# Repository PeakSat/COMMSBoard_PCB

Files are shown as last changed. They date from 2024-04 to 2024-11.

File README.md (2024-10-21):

# SatNOGS COMMS hardware

A CubeSat format ([LibreCube Board](https://wiki.librecube.org/index.php?title=LibreCube_Board_Specification)) COMMS board.
It supports UHF and S-Band concurrent half duplex (in each band) communication.
More details could be found [here](https://gitlab.com/librespacefoundation/satnogs-comms/satnogs-comms-design-doc).

Stable versions are tagging with TBD.

## Contribute
This is a KiCAD project thus merging can be tricky.
Coordinate with project engineers before starting any changes and take look at issues.

## EDA
KiCAD 6

Requires [lsf-kicad-lib](https://gitlab.com/librespacefoundation/lsf-kicad-lib) to be installed.
Set path LSF_KICAD_LIB to point to lsf-kicad-lib folder for 3D models to appear correctly

#### Schematic
Changes in manufacturer part numbers field, footprints and designators can be merged most of the times.
Any part change, change in placement, wire placement etc cannot be merged at this point.

One exception is Hierarchical sheets provided that:

* A single person is working on a Hierarchical sheet
* Annotation is using sheet number
* Global nets are respected
* Changes in Hierarchical labels are coordinated

#### PCB
At this point any merging on PCB files must be avoided.
Also for the PCB (*.kicad_pcb) is used [LFS](https://docs.gitlab.com/ee/topics/git/lfs/) to prevent
a large size repository and to use the feature of LFS lock. The LFS lock protects the developers
to have conflicts in PCB that aren't merged. For that reason use:

```
git lfs clone
```

to clone the repository.

## Simulation
[Qucs 0.0.20](https://github.com/Qucs/qucs).

## License
Licensed under the [CERN OHLv1.2](LICENSE)


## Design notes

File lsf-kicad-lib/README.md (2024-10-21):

## Libre Space Foundation KiCad Library

This repository contains the schematic, footprint and 3D libraries maintained by the LSF KiCad library team.

Most designed from scratch. Some 3D models are Hirose downloads, and [Smisioto's](http://smisioto.no-ip.org/elettronica/kicad/kicad-en.htm) released under CC-BY-SA v3

## Usage
Clone lsf-kicad-lib and import symbol and footprint libraries to your KiCad installation  
Under `Preferences -> Configure Path` set a new environment variable named `LSF_KICAD_LIB` and set the path to the location where lsf-kicad-lib is cloned  

## Contributing
Unless you are contributing to an LSF hardware project, please consider contributing directly to [KiCad libraries](https://gitlab.com/kicad)  
Please adhere to [KLC](https://klc.kicad.org/) when creating components  
Footprint 3D models should have a path prefix of `${LSF_KICAD_LIB}/lsf-kicad-lib.3dshapes/` so a complete path would look like `${LSF_KICAD_LIB}/lsf-kicad-lib.3dshapes/One_Small_Step_For_Man-size_9.5in.wrl`

lsf-kicad-lib uses CI to test against [KLC](https://klc.kicad.org/), if CI fails but component is correct please justify the reason in your merge request

## License

Licensed under the [Creative Commons CC-BY-SA 4.0 License](LICENSE) or as referenced.

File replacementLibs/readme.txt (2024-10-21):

Miniciruits BPJC-252R+ bandpass filter footprint to be added upon creation
Add x2 new mosfet to the one channel one as well
RPL x2

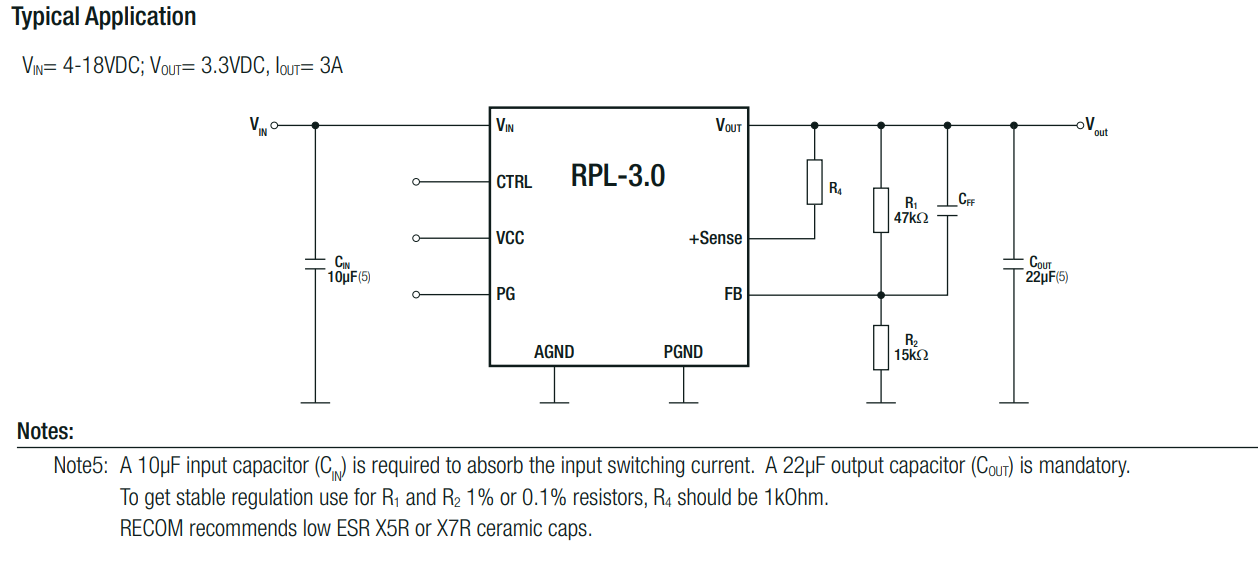
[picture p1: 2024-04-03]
3d_sources/RTL.PNG

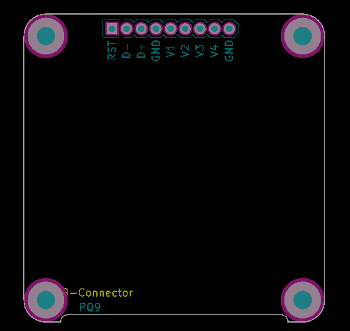
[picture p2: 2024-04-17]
lsf-kicad-lib/templates/PQ9/meta/board.png

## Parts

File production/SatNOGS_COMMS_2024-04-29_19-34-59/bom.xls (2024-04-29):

Designator,Footprint,Quantity,Value,LCSC Part #
ANT-S901,MMCX_Molex_73415-0961_Horizontal_1.6mm-PCB,1,RF 24,
ANT-U1001,MMCX_Molex_73415-0961_Horizontal_1.6mm-PCB,1,RF 09,
C1,0402,1,470n,
C1001, C1002, C1004, C1006, C1011, C1013, C1018, C1020, C1021, C1022, C1024, C1025, C1026, C1028, C1032, C1038, C1039, C1042, C1047, C1049, C1052, C1055, C612, C613, C616, C619,0402,26,100p,
C1003, C1005, C1010, C1012, C1017, C1019, C1023, C1030, C1048, C1053, C1054, C2, C31, C402, C403, C406, C408, C409, C410, C411, C412, C413, C415, C418, C501, C502, C603, C604, C605, C607, C608, C609, C701, C702, C703,0402,35,100n,
C1007, C1008, C1009, C1014, C1016, C1037, C601,0402,7,1n,
C1015,0603,1,220pF,
C1027,0402,1,2p,
C1029, C1034, C1035,0402,3,10n,
C1031,0402,1,62p,
C1036,T495C,1,10u,
C1040,0402,1,24p,
C1043,0402,1,3.3p,
C1046, C606, C610, C611,0402,4,1u,
C1050, C1051, C504,0805,3,10u,
C17, C18, C19, C20, C21, C6,0603,6,1n,
C201, C202, C531, C9,0603,4,100n,
C23, C24, C25, C27, C28, C3,0805,6,22uF,
C29, C7,0805,2,6.8u,
C404, C405, C407,1206,3,4.7u,
C419, C420,1206,2,2.2u,
C421, C422,0402,2,12p,
C5,0603,1,10u,
C506, C512,0805,2,100n,
C510,0402,1,2.2n,
C513, C516,0805,2,22u,
C529, C533,0603,2,1u,
C602,0402,1,10p,
D401,0402,1,PE14,
D402,0402,1,PE15,
D501,0805,1,3.6V,
D502,0402,1,3V3,
FB1001, FB401,0603,2,Ferrite_Bead,
FID1, FID2, FID3, FID4, FID5, FID6,Fiducial_1mm_Mask2mm,6,Fiducial,
FL2,SF2446E,1,SF2446E,
IC1,B1601,1,B1601,
J1, J2,Molex_Pico-Lock_504050-0491_1x04-1MP_P1.50mm_Horizontal,2,Conn_01x04,
J102,ESQ-126-39-x-D,1,Η1,
J103,ESQ-126-39-x-D,1,Η2,
L1001, L1002,0402,2,120n,
L1003, L1005, L1009,0402,3,68n,
L1004,0402,1,3.2n,
L1006,0402,1,18n,
L1007,0402,1,8.2n,
L1008,0402,1,47n,
L2,L_Abracon_ASPI-0530HI,1,2.2u,
L3,0805,1,0u,
L501,L_Bourns_SRN6045TA,1,4.7u,
Q1, Q2,SQJ910AEPT1_GE3,2,SQJB90EP-T1_GE3,
Q3,SOT95P230X110-3N,1,PMV28XPEAR,
Q401,SOT-23,1,FDN308P,
R1, R1030, R1031, R402, R605,0402,5,100k,
R10, R1004, R1005, R1006, R1007, R1008, R1009, R1012, R1014, R1020, R1021, R1022, R1024, R405, R606,0402,15,0,
R1001, R1002,0402,2,82,
R1003,0402,1,52.3,
R1010, R1011, R1029, R11, R3, R4, R406, R509, R533, R534, R6, R603, R8, R9,0402,14,10k,
R1013, R1015, R1023, R401,0402,4,1k,
R1016,0402,1,412,
R1017,0402,1,240,
R1019,0402,1,280,
R1025,0402,1,2.2k,
R1028,0402,1,33k,
R1032,0402,1,374k,
R1033,0402,1,110k,
R12, R407,0402,2,DNP,
R13, R14, R17, R18,0402,4,5k,
R15, R16, R502, R504, R507,0603,5,100k,
R2,0402,1,18.2k,
R201, R202, R522,0603,3,10k,
R203, R204,0603,2,120,
R403,0402,1,4.7k,
R5,0402,1,25.5k,
R501,0603,1,200k,
R503,0603,1,345k,
R508,0603,1,620k,
R510,0603,1,73.2k,
R513,0603,1,706k,
R515, R516,0603,2,2.2k,
R520,0603,1,30,
R521,0603,1,30.9k,
R529, R530, R531, R532,0805,4,0.02,
R537,0402,1,330,
R604,0402,1,470,
R7,0402,1,4.87k,
R701, R702, R703,0402,3,500,
RN401,R_Array_Convex_2x0402,1,330,
RN601,R_Array_Convex_4x0402,1,470,
RN603,R_Array_Convex_2x0402,1,R_Pack02,
T1001, T1002,ATB2012,2,Transformer_1P_1S,
U1,LQFP-100_14x14mm_P0.5mm,1,STM32H743VITx,
U1001,QFN-16-1EP_4x4mm_P0.65mm_EP2.1x2.1mm_ThermalVias,1,AD8318,
U1002,LFCSP-24-1EP_4x4mm_P0.5mm_EP2.3x2.3mm_ThermalVias,1,ADL5330,
U1003, U1004,Fairchild_MicroPak-6_1.0x1.45mm_P0.5mm,2,NC7SB3157L6X,
U1006,QFN-24-1EP_4x4mm_P0.5mm_EP2.7x2.7mm_ThermalVias,1,TQP7M9106,
U1009,DFN-8-1EP_2x2mm_P0.5mm_EP1.05x1.75mm,1,TSV912IQ2T,
U1012,GE0805C-2,1,LFCG-490+,
U1013,DFN-8-1EP_2x2mm_P0.5mm_EP0.7x1.6mm,1,TQP3M9036,
U1014, U603,SOT-553,2,NL17SV04XV5T2G,
U1015,GE0805C-2,1,LFCG-1400+,
U1016, U1017,MLP-8,2,FPF2701,
U1018,IDT_NEG-12-1EP_2x2mm_P0.5mm_EP1.1x1.1mm_ThermalVias,1,F2972,
U3,Texas_VQFN-10-HR_2x2_Pitch0.5mm,1,TPS62913,
U4, U5,SOT-23-8,2,TCAN337G,
U401,BGA-153_13.0mmx11.5mm_P0.5mm,1,SDINBDG4-8G,
U404,OSC_ECS-TXO-2520-33-120-AN-TR,1,ECS-TXO-2520-33-120-AN-TR,
U501, U502,Maxim_T833-2_TDFN-8-1EP_3x3mm_P0.65mm_EP1.5x2.3mm,2,MAX6497,
U504,SOT-23-6,1,TPS56339,
U508,WSON-6-1EP_2x2mm_P0.65mm_EP1x1.6mm_ThermalVias,1,LP5912-3.3DRV,
U509,Texas_RGV_S-PVQFN-N16_EP2.1x2.1mm,1,INA3221,
U6,QFN-14-1EP_1.60x1.60mm_P0.40mm_EP0.74x0.74mm,1,SKY13421-486LF,
U601,KT1612,1,KT1612A,
U602,QFN-48-1EP_7x7mm_P0.5mm_EP5.6x5.6mm,1,AT86RF215,
U701, U702, U703,WSON-6-1EP_2x2mm_P0.65mm_EP1x1.6mm,3,TMP117,
Y401,Crystal_SMD_3215-2Pin_3.2x1.5mm,1,32768Hz,

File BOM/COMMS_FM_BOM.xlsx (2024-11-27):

Designator | Footprint | Quantity | Value
ANT-S901 | MMCX_Molex_73415-0961_Horizontal_1.6mm-PCB | 1 | RF 24 | 73415-0961 (https://gr.mouser.com/ProductDetail/Molex/73415-0961?qs=LDM2r2BBpnbP9ohwHUReTQ%3D%3D)
ANT-U1001 | MMCX_Molex_73415-0961_Horizontal_1.6mm-PCB | 1 | RF 09 | 73415-0961 (https://gr.mouser.com/ProductDetail/Molex/73415-0961?qs=LDM2r2BBpnbP9ohwHUReTQ%3D%3D)
C1 | 402 | 1 | 2.2u | MSAST105CB5225KFNA01 (https://eu.mouser.com/ProductDetail/TAIYO-YUDEN/MSAST105CB5225KFNA01?qs=tlsG%2FOw5FFgp%2Fj%252BcBdp0SQ%3D%3D)
C1001, C1002, C1004, C1006, C1011, C1013, C1018, C1020, C1021, C1022, C1024, C1025, C1026, C1028, C1032, C1038, C1039, C1042, C1047, C1049, C1052, C1055, C612, C613, C616, C619 | 0402 | 26 | 100p | CBR04C101J3GAC (https://gr.mouser.com/ProductDetail/KEMET/CBR04C101J3GAC?qs=kpVq%2FgIAs50lnV8B4851AQ%3D%3D)
C1003, C1005, C1010, C1012, C1017, C1019, C1023, C1030, C1048, C1053, C1054, C2, C31, C402, C403, C406, C408, C409, C410, C411, C412, C413, C415, C418, C501, C502, C603, C604, C605, C607, C608, C609, C701, C702, C703 | 0402 | 35 | 100n | C0402C104K4RACTU (https://gr.mouser.com/ProductDetail/KEMET/C0402C104K4RACTU?qs=DBJr%252BvBUjU54jK7d4uAeew%3D%3D)
C1007, C1008, C1009, C1014, C1016, C1037, C601 | 0402 | 7 | 1n | C0402C102K8RACAUTO (https://gr.mouser.com/ProductDetail/KEMET/C0402C102K8RACAUTO?qs=PqoDHHvF64%252Bcvfiy0YO9RQ%3D%3D)
C1015 | 0603 | 1 | 220pF | CL10C221JB8NNNC (https://gr.mouser.com/ProductDetail/Samsung-Electro-Mechanics/CL10C221JB8NNNC?qs=349EhDEZ59pzGXg3weaqwg%3D%3D)
C1027 | 0402 | 1 | 2p | GJM1555C1H2R0WB01D (https://gr.mouser.com/ProductDetail/Murata-Electronics/GJM1555C1H2R0WB01D?qs=YLLXL5qGyDstO156VbiHGA%3D%3D)
C1029, C1034, C1035 | 0402 | 3 | 10n | C0402C103K9RACTU (https://gr.mouser.com/ProductDetail/KEMET/C0402C103K9RACTU?qs=DBJr%252BvBUjU6xorlRi5IJdg%3D%3D)
C1031 | 0402 | 1 | 62p | 04025A620FAT2A (https://gr.mouser.com/ProductDetail/KYOCERA-AVX/04025A620FAT2A?qs=Wf75Zj%252Bm1TOgugGJIn7eTg%3D%3D)
C1036 | T495C | 1 | 10u | T495C106K035ATE400 (https://gr.mouser.com/ProductDetail/KEMET/T495C106K035ATE400?qs=MYVaeE1wThLltmp5qaw8IA%3D%3D)
C1040 | 0402 | 1 | 24p | 04025U240FAT2A (https://gr.mouser.com/ProductDetail/KYOCERA-AVX/04025U240FAT2A?qs=ZwvTZoB9SO%2FwGwGLwPpjgw%3D%3D)
C1043 | 0402 | 1 | 3.3p | GJM1555C1H3R3WB01D (https://gr.mouser.com/ProductDetail/Murata-Electronics/GJM1555C1H3R3WB01D?qs=YLLXL5qGyDt2ejtN1v%252B1AA%3D%3D)
C1046, C606, C610, C611 | 0402 | 4 | 1u | C0402C105K8PAC7411 (https://gr.mouser.com/ProductDetail/KEMET/C0402C105K8PAC7411?qs=2FIyTMJ0hNmV%2F7SAMXtJQQ%3D%3D)
C1050, C1051, C504 | 0805 | 3 | 10u | EMK212BB7106KG-T (https://gr.mouser.com/ProductDetail/TAIYO-YUDEN/EMK212BB7106KG-T?qs=vF%252B8ahGVilemLVRka0hELA%3D%3D)
C17, C18, C19, C20, C21, C6 | 0603 | 6 | 1n | C0603X102K5GACAUTO (https://gr.mouser.com/ProductDetail/KEMET/C0603X102K5GACAUTO?qs=Rp5uXu7WBW%2FQ943CZtK%2F6w%3D%3D)
C201, C202, C531, C9 | 0603 | 4 | 100n | C0603C104K9RACTU (https://gr.mouser.com/ProductDetail/KEMET/C0603C104K9RACTU?qs=7q2aiX3GdliuPZzPpldOsA%3D%3D)
C23, C24, C25, C27, C28, C3 | 0805 | 6 | 22uF | GRM21BR61A226ME44L (https://gr.mouser.com/ProductDetail/Murata-Electronics/GRM21BR61A226ME44L?qs=eeBpzGFlv%252B8tSfxib2AMhw%3D%3D)
C29, C7 | 0805 | 2 | 6.8u | C2012X5R1E685K125AC (https://gr.mouser.com/ProductDetail/TDK/C2012X5R1E685K125AC?qs=LcTL%2F5vFEzGU8HZPTu5zsg%3D%3D)
C404, C405, C407 | 1206 | 3 | 4.7u | TAJA475K016R (https://gr.mouser.com/ProductDetail/KYOCERA-AVX/TAJA475K016RNJ?qs=QtLZGLLAmDYIMcNbe5r3xw%3D%3D)
C419, C420 | 1206 | 2 | 2.2u | AC1206KKX7R7BB225 (https://gr.mouser.com/ProductDetail/YAGEO/AC1206KKX7R7BB225?qs=eP2BKZSCXI6d%2Fne9Jk0GEA%3D%3D)
C421, C422 | 0402 | 2 | 12p | CBR04C120F3GAC (https://gr.mouser.com/ProductDetail/KEMET/CBR04C120F3GAC?qs=kpVq%2FgIAs52ttHbXJFjLsg%3D%3D)
C5 | 0603 | 1 | 10u | EMK107BC6106MA-T (https://gr.mouser.com/ProductDetail/TAIYO-YUDEN/EMK107BC6106MA-T?qs=VWNNG7jHlrLjpV1w%2FJc9eQ%3D%3D)
C506, C512 | 0805 | 2 | 100n | C0805C104M5RACTU (https://gr.mouser.com/ProductDetail/KEMET/C0805C104M5RACTU?qs=VOOUd%252Bza08qHu13WgNByHQ%3D%3D)
C510 | 0402 | 1 | 2.2n | CGA2B2X7R1H222K050BA (https://gr.mouser.com/ProductDetail/TDK/CGA2B2X7R1H222K050BA?qs=NRhsANhppD%2Fb%2FoKooR%252BeFw%3D%3D)
C513, C516 | 0805 | 2 | 22u | GRM21BR61A226ME44L (https://gr.mouser.com/ProductDetail/Murata-Electronics/GRM21BR61A226ME44L?qs=eeBpzGFlv%252B8tSfxib2AMhw%3D%3D)
C529, C533 | 0603 | 2 | 1u | EMK107B7105KA-T (https://gr.mouser.com/ProductDetail/TAIYO-YUDEN/EMK107B7105KA-T?qs=I6KAKw0tg2zS1zj87Lm%2FxQ%3D%3D)
C602 | 0402 | 1 | 10p | C0402C100C8GACTU (https://gr.mouser.com/ProductDetail/KEMET/C0402C100C8GACTU?qs=v7s4VpRpa0t2l6BHkID7%2Fw%3D%3D)
D401 | 0402 | 1 | PE14 | FHA1105P-TR (https://gr.mouser.com/ProductDetail/Stanley-Electric/FHA1105P-TR?qs=byeeYqUIh0MAYVMdncV%252BvA%3D%3D)
D402 | 0402 | 1 | PE15 | FHA1105P-TR (https://gr.mouser.com/ProductDetail/Stanley-Electric/FHA1105P-TR?qs=byeeYqUIh0MAYVMdncV%252BvA%3D%3D)
D501 | 0805 | 1 | 3.6V | BZY55B3V6 RBG (https://gr.mouser.com/ProductDetail/Taiwan-Semiconductor/BZY55B3V6-RBG?qs=mAH9sUMRCtv1hjtg7HbTxw%3D%3D)
D502 | 0402 | 1 | 3V3 | APHHS1005LQBC/D-V (https://gr.mouser.com/ProductDetail/Kingbright/APHHS1005LQBC-D-V?qs=WbpYJYa8y32aFVn6IIj1Dg%3D%3D)
FB1001, FB401 | 0603 | 2 | Ferrite_Bead | BLM18KG331SN1D (https://gr.mouser.com/ProductDetail/Murata-Electronics/BLM18KG331SN1D?qs=rvfpa0%252BU10NzC2vi4JWfgQ%3D%3D)
FL2 | RF1419D | 1 | RF1419D | RF1419D (https://gr.mouser.com/ProductDetail/RFMi/RF1419D?qs=zW32dvEIR3tUQ4hxASYaKw%3D%3D)
IC1 | B1601 | 1 | Orion B16 | GNSS module | Comment: To be placed only on the FM
J1, J2 | Molex_Pico-Lock_504050-0491_1x04-1MP_P1.50mm_Horizontal | 2 | Conn_01x04 | 504050-0491 (https://gr.mouser.com/ProductDetail/Molex/504050-0491?qs=yXHQdf%252Bjwlut3yyE1%252ByhMA%3D%3D)
J102 | ESQ-126-39-x-D | 1 | Η1 | ESQ-126-48-G-D-LL (https://www.digikey.lu/en/products/detail/samtec-inc/ESQ-126-48-G-D-LL/7094695)
J103 | ESQ-126-39-x-D | 1 | Η2 | ESQ-126-48-G-D-LL (https://www.digikey.lu/en/products/detail/samtec-inc/ESQ-126-48-G-D-LL/7094695)
L1001, L1002 | 0402 | 2 | 120n | LQG15WHR12G02D (https://gr.mouser.com/ProductDetail/Murata-Electronics/LQG15WHR12G02D?qs=rkhjVJ6%2F3EIx7JCOrOt0jQ%3D%3D)
L1003, L1005, L1009 | 0402 | 3 | 68n | MHQ1005P68NGTD25 (https://gr.mouser.com/ProductDetail/TDK/MHQ1005P68NGTD25?qs=J8wJ95O2yNKke5XTsKZiRQ%3D%3D)
L1004 | 0402 | 1 | 3.2n | LQG15WZ3N2B02D (https://gr.mouser.com/ProductDetail/Murata-Electronics/LQG15WZ3N2B02D?qs=rkhjVJ6%2F3EIZ%252BUOS4bnJ5g%3D%3D)
L1006 | 0402 | 1 | 18n | LQW15AN18NJ80D (https://gr.mouser.com/ProductDetail/Murata-Electronics/LQW15AN18NJ80D?qs=hNud%2FORuBR3MthCsSHMoHQ%3D%3D)
L1007 | 0402 | 1 | 8.2n | MHQ1005P8N2GT000 (https://gr.mouser.com/ProductDetail/TDK/MHQ1005P8N2GT000?qs=u4%252BEJ9urDAQClJN4T%2Ff%252BGw%3D%3D)
L1008 | 0402 | 1 | 47n | AISC-0402-47NG-T (https://gr.mouser.com/ProductDetail/ABRACON/AISC-0402-47NG-T?qs=dtFCtVqVXWePKsh6WPotjA%3D%3D)
L2 | L_Abracon_ASPI-0530HI | 1 | 2.2u | ASPI-0520LR-2R2M-T2 (https://gr.mouser.com/ProductDetail/ABRACON/ASPI-0520LR-2R2M-T2?qs=bWAYEm3xoCbh1TG6qbeZrA%3D%3D)
L3 | 0805 | 1 | 0u | 782853200 (https://gr.mouser.com/ProductDetail/Wurth-Elektronik/782853200?qs=sBf%2Fb4nBSle7OloWbfgdIw%3D%3D)
L501 | L_Bourns_SRN6045TA | 1 | 4.7u | SRN6045-4R7Y (https://gr.mouser.com/ProductDetail/Bourns/SRN6045-4R7Y?qs=opBjA1TV902tB4tumIiZhg%3D%3D)
Q1, Q2 | SQJ910AEPT1_GE3 | 2 | SQJB90EP-T1_GE3 | SQJB90EP-T1_GE3 (https://gr.mouser.com/ProductDetail/Vishay-Semiconductors/SQJB90EP-T1_GE3?qs=EBLjwc9jJJtSPXvpvmcSow%3D%3D)
Q3 | SOT95P230X110-3N | 1 | PMV28XPEAR | PMV28XPEAR (https://gr.mouser.com/ProductDetail/Nexperia/PMV28XPEAR?qs=W%2FMpXkg%252BdQ6VcRCVGMTksA%3D%3D)
Q401 | SOT-23 | 1 | FDN308P | FDN308P (https://gr.mouser.com/ProductDetail/onsemi-Fairchild/FDN308P?qs=GeD7q9OHBPyTnI9LJIlNJQ%3D%3D)
R1, R1030, R1031, R402, R605 | 0402 | 5 | 100k | CR0402-FX-1003GLF (https://gr.mouser.com/ProductDetail/Bourns/CR0402-FX-1003GLF?qs=URDPQ%2Fj0cz1ZruPSJQ7fsA%3D%3D)
R10, R1004, R1005, R1006, R1007, R1008, R1009, R1012, R1014, R1020, R1021, R1022, R1024, R405, R606 | 0402 | 15 | 0 | RC0402JR-070R (https://gr.mouser.com/ProductDetail/YAGEO/RC0402JR-070RP?qs=oypCK0zG324njv6h4dM%2FBg%3D%3D)
R1001, R1002 | 0402 | 2 | 82 | ERA-2AEB820X (https://gr.mouser.com/ProductDetail/Panasonic/ERA-2AEB820X?qs=YFwoyZoVY0jWB%2FWuuQzFhw%3D%3D)
R1003 | 0402 | 1 | 52.3 | RG1005P-52R3-B-T5 (https://gr.mouser.com/ProductDetail/Susumu/RG1005P-52R3-B-T5?qs=v5GkGT6DDHiy8ArKIHE1bw%3D%3D)
R1010, R1011, R1029, R11, R3, R4, R406, R509, R533, R534, R6, R603, R8, R9 | 0402 | 14 | 10k | CRCW040210K0FKEDC (https://gr.mouser.com/ProductDetail/Vishay-Dale/CRCW040210K0FKEDC?qs=E3Y5ESvWgWPiNLcGzwCGPg%3D%3D)
R1013, R1015, R1023, R401 | 0402 | 4 | 1k | CRCW04021K00FKEDC (https://gr.mouser.com/ProductDetail/Vishay-Dale/CRCW04021K00FKEDC?qs=E3Y5ESvWgWMj5mY%252BhDIyqg%3D%3D)
R1016 | 0402 | 1 | 412 | CRCW0402412RFKED (https://gr.mouser.com/ProductDetail/Vishay-Dale/CRCW0402412RFKED?qs=FaFwO5VmXOIp6VCgzV9Dxg%3D%3D)
R1017 | 0402 | 1 | 240 | CRCW0402240RFKEDC (https://gr.mouser.com/ProductDetail/Vishay-Dale/CRCW0402240RFKEDC?qs=E3Y5ESvWgWOlhgV8l94Qkw%3D%3D)
R1019 | 0402 | 1 | 280 | RC0402FR-07280RL (https://gr.mouser.com/ProductDetail/YAGEO/RC0402FR-07280RL?qs=f9DM49H8yrNOsmUU2z7A4A%3D%3D)
R1025 | 0402 | 1 | 2.2k | CRCW04022K20JNEDC (https://gr.mouser.com/ProductDetail/Vishay-Dale/CRCW04022K20JNEDC?qs=E3Y5ESvWgWOj5R%252BsplsFLw%3D%3D)
R1028 | 0402 | 1 | 33k | CR0402-FX-3302GLF (https://gr.mouser.com/ProductDetail/Bourns/CR0402-FX-3302GLF?qs=SFHnMgm9Isze0zS5GpsQzw%3D%3D)
R1032 | 0402 | 1 | 374k | CRCW0402374KFKED (https://gr.mouser.com/ProductDetail/Vishay-Dale/CRCW0402374KFKED?qs=1XGAtBqYNz57mwAP8KKAqw%3D%3D)
R1033 | 0402 | 1 | 110k | CRCW0402110KFKED (https://gr.mouser.com/ProductDetail/Vishay-Dale/CRCW0402110KFKED?qs=rlE3Te1NifyoK3%2FXIabNHA%3D%3D)
R12, R407 | 0402 | 2 | DNP
R13, R14, R17, R18 | 0402 | 4 | 5k | RC0402FR-075KL (https://gr.mouser.com/ProductDetail/YAGEO/RC0402FR-075KL?qs=9h0bZHM%2F3zL5adZvfm%252BR4Q%3D%3D)
R504 | 0603 | 1 | 100k | RN73H1JTTD1003F50 (https://eu.mouser.com/ProductDetail/KOA-Speer/RN73H1JTTD1003F50?qs=0hon8nwgHra%252Ba4k3Zp48xw%3D%3D)
R15, R16, R502, R504, R507 | 0603 | 5 | 100k | ERJ-3EKF1003V (https://gr.mouser.com/ProductDetail/Panasonic/ERJ-3EKF1003V?qs=H7k1u0Mp9JSqh2R2gj46DA%3D%3D)
R2 | 0402 | 1 | 18.2k | CRCW040218K2FKED (https://gr.mouser.com/ProductDetail/Vishay-Dale/CRCW040218K2FKED?qs=QPqDnsKvzKctMPTti4xZ7g%3D%3D)
R201, R202, R522 | 0603 | 3 | 10k | CRCW060310K0FKECC (https://gr.mouser.com/ProductDetail/Vishay-Dale/CRCW060310K0FKECC?qs=wd5RIQLrsJjYJGKL%252BLOtbQ%3D%3D)
R203, R204 | 0603 | 2 | 120 | ERJ-3EKF1200V (https://gr.mouser.com/ProductDetail/Panasonic/ERJ-3EKF1200V?qs=iBwFsHVUAOfkZ4Bj0qjBGg%3D%3D)
R403 | 0402 | 1 | 4.7k | CRCW04024K70FKEDC (https://gr.mouser.com/ProductDetail/Vishay-Dale/CRCW04024K70FKEDC?qs=E3Y5ESvWgWMhkkkEGGyyBQ%3D%3D)
R5 | 0402 | 1 | 25.5k | CRCW040225K5FKED (https://gr.mouser.com/ProductDetail/Vishay-Dale/CRCW040225K5FKED?qs=hD42E%2F8yzjq2MGDaErf%252BPQ%3D%3D)
R501 | 0603 | 1 | 200k | ERJ-H3ED2003V (https://gr.mouser.com/ProductDetail/Panasonic/ERJ-H3ED2003V?qs=eP2BKZSCXI7daGmcQhIBgg%3D%3D)
R503 | 0603 | 1 | 345k | RN731JTTD3443F100 (https://gr.mouser.com/ProductDetail/KOA-Speer/RN731JTTD3443F100?qs=F5djdNSOT4bwjyqVk7yJug%3D%3D)
R508 | 0603 | 1 | 620k | CPF0603B620KE (https://gr.mouser.com/ProductDetail/TE-Connectivity-Holsworthy/CPF0603B620KE?qs=gt1LBUVyoHkO9kiWGgxegA%3D%3D)
R510 | 0603 | 1 | 73.2k | RT0603FRE0773K2L (https://gr.mouser.com/ProductDetail/YAGEO/RT0603FRE0773K2L?qs=4Yf0coX8WGHmhZiQKKa7fg%3D%3D)
R513 | 0603 | 1 | 706k | RN73H1JTTD7063D100 (https://gr.mouser.com/ProductDetail/KOA-Speer/RN73H1JTTD7063D100?qs=VuQ0gRj%2FiB4rvIsmRvyBAA%3D%3D)
R515, R516 | 0603 | 2 | 2.2k | CR0603-JW-222ELF (https://gr.mouser.com/ProductDetail/Bourns/CR0603-JW-222ELF?qs=1ekQ6LclRXWKYqsntfXI1g%3D%3D)
R520 | 0603 | 1 | 30 | RC0603FR-0730RL (https://gr.mouser.com/ProductDetail/YAGEO/RC0603FR-0730RL?qs=0yPvnVz5%2FmrjDQM%2FBqZ6fQ%3D%3D)
R521 | 0603 | 1 | 30.9k | ERJ-U03F3092V (https://gr.mouser.com/ProductDetail/Panasonic/ERJ-U03F3092V?qs=pdFhdcvjjgjUMWv%2Fr%2Fwx8w%3D%3D)
R529, R530, R531, R532 | 0805 | 4 | 0.02 | RCWH080520L0FMEA (https://gr.mouser.com/ProductDetail/Vishay-Dale/RCWH080520L0FMEA?qs=QEzMiVqgwc3cRF46dIlgBg%3D%3D)
R537 | 0402 | 1 | 330 | ERA-2AED331X (https://gr.mouser.com/ProductDetail/Panasonic/ERA-2AED331X?qs=nho8PGNfA6ogbDEk0GXBJg%3D%3D)
R604 | 0402 | 1 | 470 | CRCW0402470RFKEDC (https://gr.mouser.com/ProductDetail/Vishay-Dale/CRCW0402470RFKEDC?qs=E3Y5ESvWgWMHurQeeaZqDg%3D%3D)
R7 | 0402 | 1 | 4.87k | CRCW04024K87FKEDC (https://gr.mouser.com/ProductDetail/Vishay-Dale/CRCW04024K87FKEDC?qs=E3Y5ESvWgWPRVWWz5md27Q%3D%3D)
R701, R702, R703 | 0402 | 3 | 500 | RR0510P-511-D (https://gr.mouser.com/ProductDetail/Susumu/RR0510P-511-D?qs=nCAm%252BcMdy9ztGQsPnUEJRw%3D%3D)
RN401 | R_Array_Convex_2x0402 | 1 | 330 | EXB-24V331JX (https://gr.mouser.com/ProductDetail/Panasonic/EXB-24V331JX?qs=WwqriLBepZvGrh8Fm9ZyEg%3D%3D)
RN601 | R_Array_Convex_4x0402 | 1 | 470 | EXB-28V471JX (https://gr.mouser.com/ProductDetail/Panasonic/EXB-28V471JX?qs=cttFivMKqWzjxnZBTe8wzg%3D%3D)
RN603 | R_Array_Convex_2x0402 | 1 | R_Pack02 | EXB-24VR000X (https://gr.mouser.com/ProductDetail/Panasonic/EXB-24VR000X?qs=oE3VwAv%2FYtkhBt%252BP4TTG6Q%3D%3D)
T1001, T1002 | ATB2012 | 2 | Transformer_1P_1S | ATB2012-50011-T000 (https://gr.mouser.com/ProductDetail/TDK/ATB2012-50011-T000?qs=tfZGHB2PWd0kY5zZEl3yJA%3D%3D)
U1 | LQFP-100_14x14mm_P0.5mm | 1 | STM32H743VITx
U1001 | QFN-16-1EP_4x4mm_P0.65mm_EP2.1x2.1mm_ThermalVias | 1 | AD8318 | AD8318ACPZ-REEL7 (https://gr.mouser.com/ProductDetail/Analog-Devices/AD8318ACPZ-REEL7?qs=%2FtpEQrCGXCw0ZYFmnJA9Lg%3D%3D)
U1002 | LFCSP-24-1EP_4x4mm_P0.5mm_EP2.3x2.3mm_ThermalVias | 1 | ADL5330 | ADL5330ACPZ-REEL7 (https://gr.mouser.com/ProductDetail/Analog-Devices/ADL5330ACPZ-REEL7?qs=BpaRKvA4VqHKSaFmsJzGUQ%3D%3D)
U1003, U1004 | Fairchild_MicroPak-6_1.0x1.45mm_P0.5mm | 2 | NC7SB3157L6X | NC7SB3157L6X (https://www.digikey.gr/en/products/detail/onsemi/NC7SB3157L6X/1052765)
U1006 | QFN-24-1EP_4x4mm_P0.5mm_EP2.7x2.7mm_ThermalVias | 1 | TQP7M9106 | TQP7M9106 (https://gr.mouser.com/ProductDetail/Qorvo/TQP7M9106?qs=ZyJ8JrQCoIZWZMWEw%252BwsMg%3D%3D)
U1009 | DFN-8-1EP_2x2mm_P0.5mm_EP1.05x1.75mm | 1 | TSV912IQ2T | TSV912IQ2T (https://gr.mouser.com/ProductDetail/STMicroelectronics/TSV912IQ2T?qs=vV0pr1uq7fCYSLiIBwfwNg%3D%3D)
U1012 | GE0805C-2 | 1 | LFCG-490+ | LFCG-490+ (https://gr.mouser.com/ProductDetail/Mini-Circuits/LFCG-490%2b?qs=vmHwEFxEFR%252BNH1d71kamjA%3D%3D)
U1013 | DFN-8-1EP_2x2mm_P0.5mm_EP0.7x1.6mm | 1 | TQP3M9036 | TQP3M9036 (https://gr.mouser.com/ProductDetail/Qorvo/TQP3M9036?qs=73ok1p1Z9vuHVw3N%2FSkE8w%3D%3D)
U1014, U603 | SOT-553 | 2 | NL17SV04XV5T2G | NL17SV04XV5T2G (https://www.digikey.gr/en/products/detail/onsemi/NL17SV04XV5T2G/1484408)
U1015 | GE0805C-2 | 1 | LFCG-1400+ | LFCG-1400+ (https://gr.mouser.com/ProductDetail/Mini-Circuits/LFCG-1400%2b?qs=xZ%2FP%252Ba9zWqYyOJMy40Q8cg%3D%3D)
U1016, U1017 | MLP-8 | 2 | FPF2701MPX | FPF2701MPX
U1018 | IDT_NEG-12-1EP_2x2mm_P0.5mm_EP1.1x1.1mm_ThermalVias | 1 | F2972 | F2972 (https://gr.mouser.com/ProductDetail/Renesas-Electronics/F2972NEGK?qs=1cUJgmOA5Aedcy1DngO4xQ%3D%3D)
U3 | Texas_VQFN-10-HR_2x2_Pitch0.5mm | 1 | TPS62913 | TPS62913 (https://gr.mouser.com/ProductDetail/Texas-Instruments/TPS62913RPUR?qs=DRkmTr78QAQI55KgaHZCew%3D%3D)
U4, U5 | SOT-23-8 | 2 | TCAN337G | TCAN337GDCNT (https://gr.mouser.com/ProductDetail/Texas-Instruments/TCAN337GDCNT?qs=gMfM3zrbS4oQNehEF%252BRyog%3D%3D)
U401 | BGA-153_13.0mmx11.5mm_P0.5mm | 1 | SDINBDG4-8G | SDINBDG4-8G (https://gr.mouser.com/ProductDetail/SanDisk/SDINBDG4-8G?qs=5aG0NVq1C4wrY83%2Fr3SiEA%3D%3D)
U404 | OSC_ECS-TXO-2520-33-120-AN-TR | 1 | ECS-TXO-2520-33-120-AN-TR | ECS-TXO-2520-33-120-AN-TR (https://gr.mouser.com/ProductDetail/ECS/ECS-TXO-2520-33-120-AN-TR?qs=KAq9QXcE8HB8zqkkQbQ2Dw%3D%3D)
U501, U502 | Maxim_T833-2_TDFN-8-1EP_3x3mm_P0.65mm_EP1.5x2.3mm | 2 | MAX6497 | MAX6497ATA+T (https://gr.mouser.com/ProductDetail/Analog-Devices-Maxim-Integrated/MAX6497ATA%2bT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)
U504 | SOT-23-6 | 1 | TPS56339 | TPS56339DDCR (https://gr.mouser.com/ProductDetail/Texas-Instruments/TPS56339DDCR?qs=T3oQrply3y%2FnX4YgbxZYZA%3D%3D)
U508 | WSON-6-1EP_2x2mm_P0.65mm_EP1x1.6mm_ThermalVias | 1 | LP5912-3.3DRV | LP5912-3.3DRV (https://gr.mouser.com/ProductDetail/Texas-Instruments/LP5912-3.3DRVR?qs=n%252BTO0c4TDSY0RMrHlK%2FGvQ%3D%3D)
U509 | Texas_RGV_S-PVQFN-N16_EP2.1x2.1mm | 1 | INA3221 | INA3221 (https://gr.mouser.com/ProductDetail/Texas-Instruments/INA3221AQRGVRQ1?qs=F66ExNIg9rol9iKDWhbDmg%3D%3D)
U6 | QFN-14-1EP_1.60x1.60mm_P0.40mm_EP0.74x0.74mm | 1 | SKY13421-486LF | SKY13421-486LF (https://gr.mouser.com/ProductDetail/Skyworks-Solutions-Inc/SKY13421-486LF?qs=NzhwYt3CeasYvHZz%2FWhkVQ%3D%3D)
U601 | KT1612 | 1 | KT1612A | KT1612A26000AAW18TBL (https://gr.mouser.com/ProductDetail/KYOCERA-AVX/KT1612A26000AAW18TBL?qs=By6Nw2ByBD0XxPLaJI1HGw%3D%3D)
U602 | QFN-48-1EP_7x7mm_P0.5mm_EP5.6x5.6mm | 1 | AT86RF215 | AT86RF215-ZUR (https://gr.mouser.com/ProductDetail/Microchip-Technology/AT86RF215-ZUR?qs=9KdFJXLqUo9WD3U%2FPpQzxw%3D%3D)
U701, U702, U703 | WSON-6-1EP_2x2mm_P0.65mm_EP1x1.6mm | 3 | TMP117 | TMP117NAIDRVR (https://gr.mouser.com/ProductDetail/Texas-Instruments/TMP117NAIDRVR?qs=qSfuJ%252Bfl%2Fd51FgClPJTgfg%3D%3D)
Y401 | Crystal_SMD_3215-2Pin_3.2x1.5mm | 1 | 32768Hz | ABS07-32.768KHZ-7-T (https://gr.mouser.com/ProductDetail/ABRACON/ABS07-32.768KHZ-7-T?qs=2nyfZ6BV3oibNEFok2qBLA%3D%3D)

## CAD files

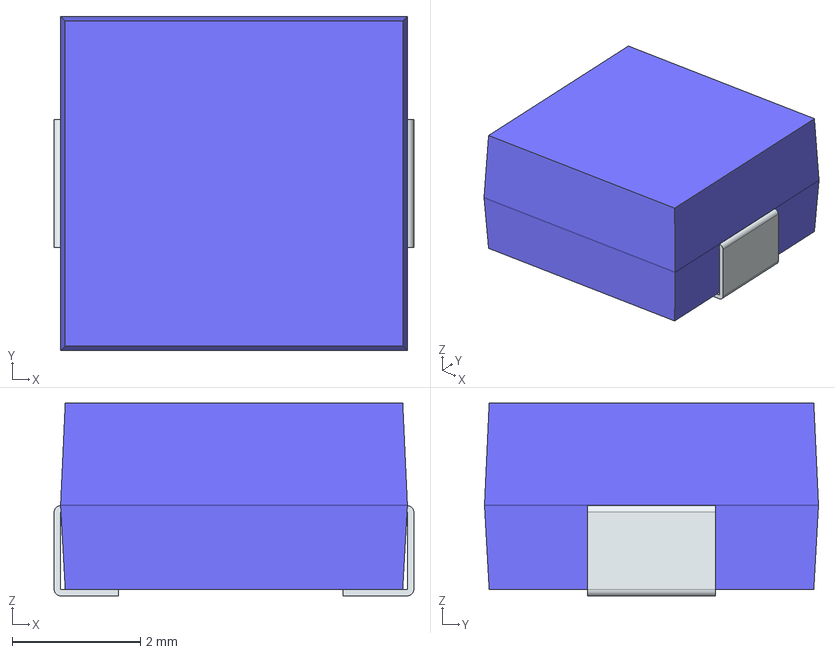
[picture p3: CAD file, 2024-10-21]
3d_sources/ASPI-0530HI-2R2M-T2/3D/ASPI-0530HI-2R2M-T2.stp
5.60 x 5.20 x 3.00 mm
FilletPin1
FilletPin2

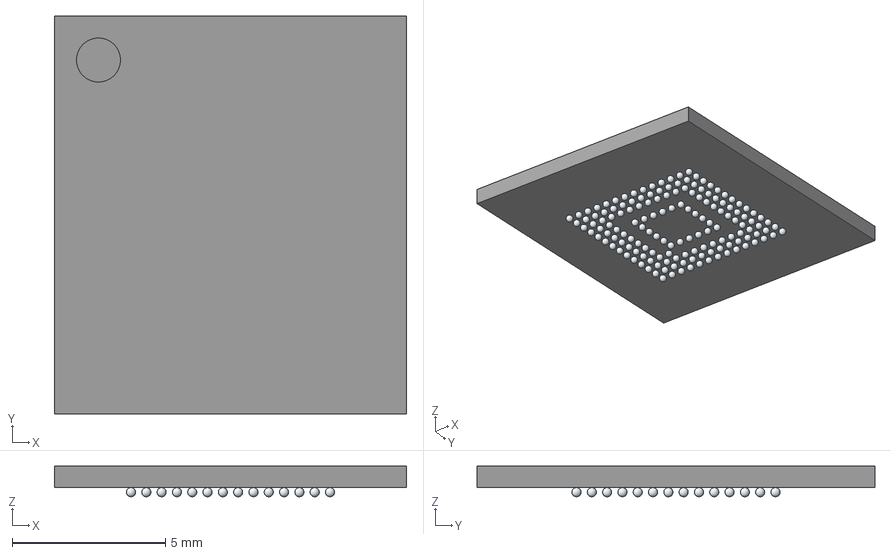
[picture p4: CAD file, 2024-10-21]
3d_sources/SDINBDG4-32G-ZA.stp
11.5 x 13.0 x 1.00 mm
A1
A2
A3
A4
A5
A6
A7
A8
A9
A10
A11
A12
A13
A14
B1
B2
B3
B4
B5
B6
B7
B8
B9
B10
B11
B12
B13
B14
C1
C2
C3
C4
C5
C6
C7
C8
C9
C10
C11
C12
C13
C14
D1
D2
D3
D4
D12
D13
D14
E1
E2
E3
E5
E6
E7
E8
E9
E10
E12
E13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

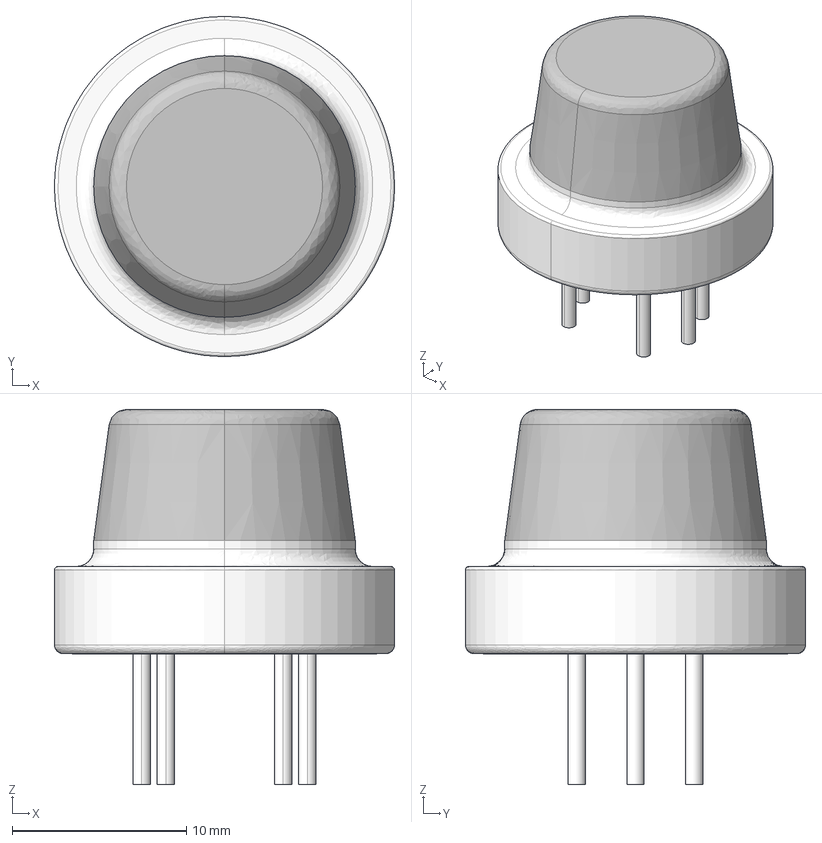
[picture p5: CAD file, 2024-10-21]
lsf-kicad-lib/3d/MQ_Sensors/MQ-131.step
19.5 x 19.5 x 21.5 mm

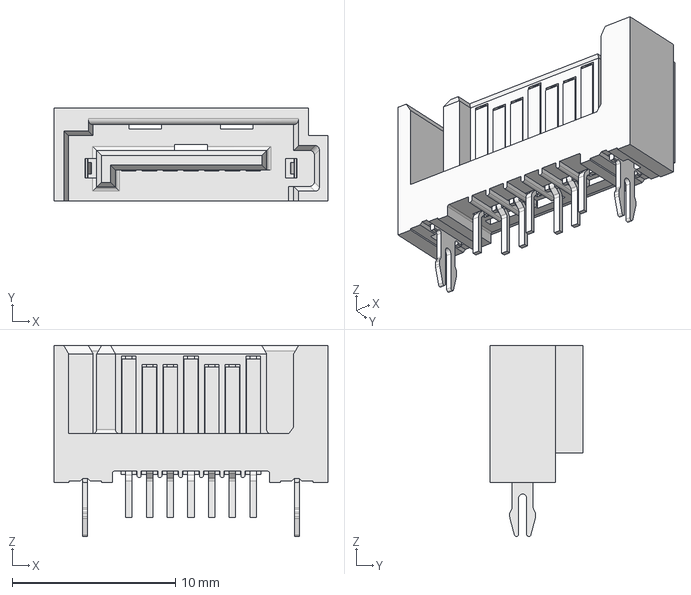
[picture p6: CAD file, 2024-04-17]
lsf-kicad-lib/3d_sources/SATA-3M-5607-5102-SH.FCStd
16.8 x 5.70 x 11.7 mm

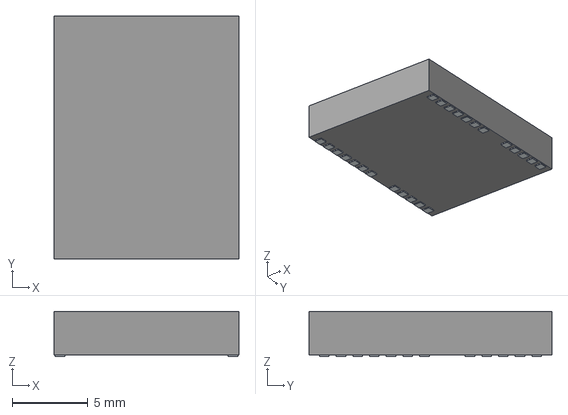
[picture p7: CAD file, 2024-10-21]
replacementLibs/Orion-B16/B16тАР01.stp
12.2 x 16.0 x 3.00 mm
Pins

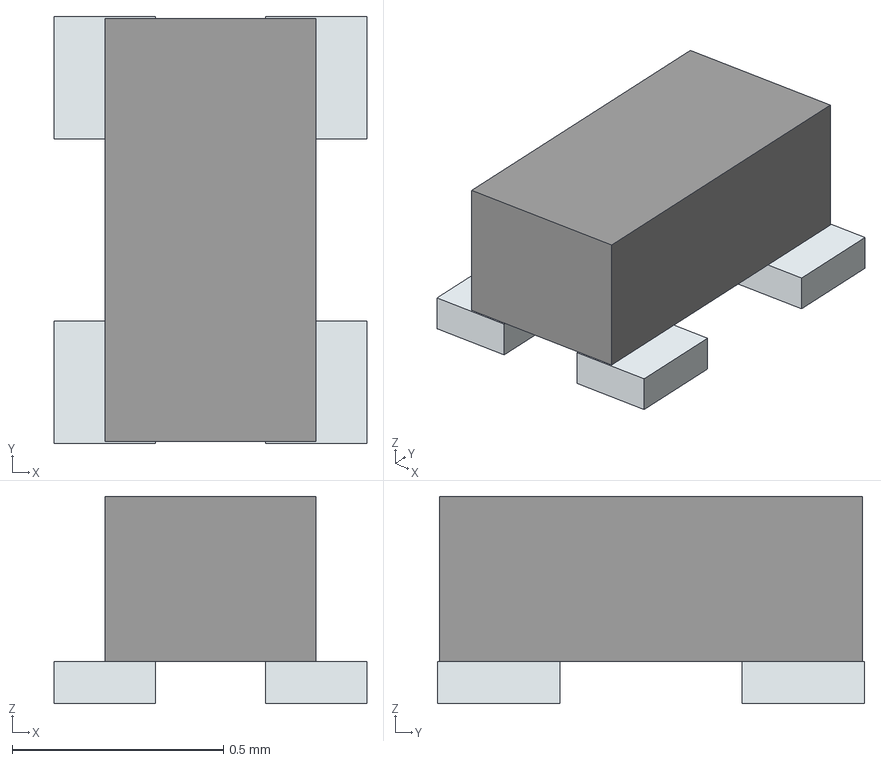
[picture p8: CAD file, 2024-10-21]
replacementLibs/PAT0510S-C-3DB-T10/PAT0510S-C-3DB-T10.stp
0.74 x 1.01 x 0.49 mm
Pins

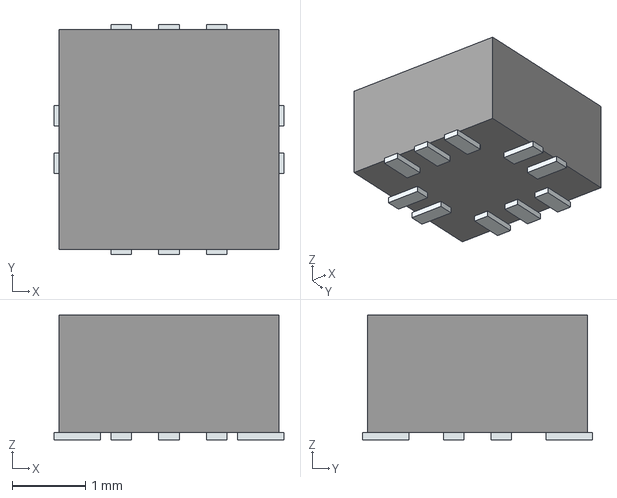
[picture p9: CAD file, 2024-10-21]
replacementLibs/RPL/RPL-3.0-CT.stp
3.13 x 3.13 x 1.70 mm
Pins

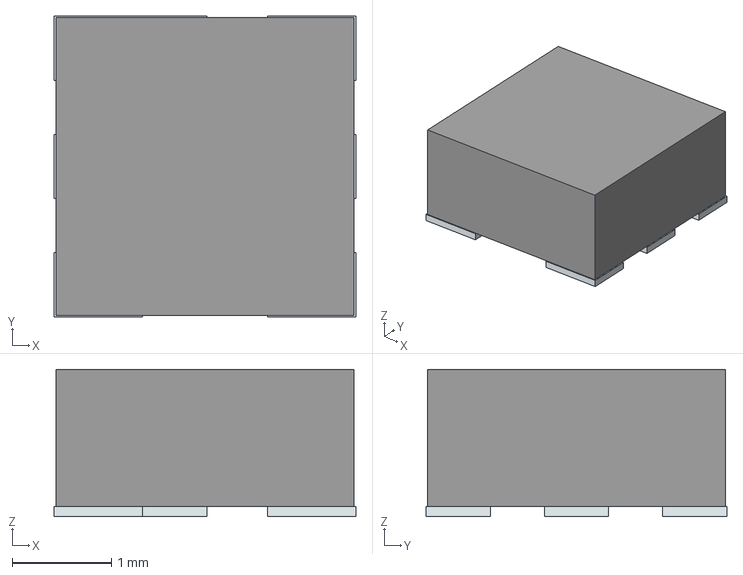
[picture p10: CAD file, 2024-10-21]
replacementLibs/SF2446E/SF2446E.stp
3.04 x 3.03 x 1.48 mm
Pins

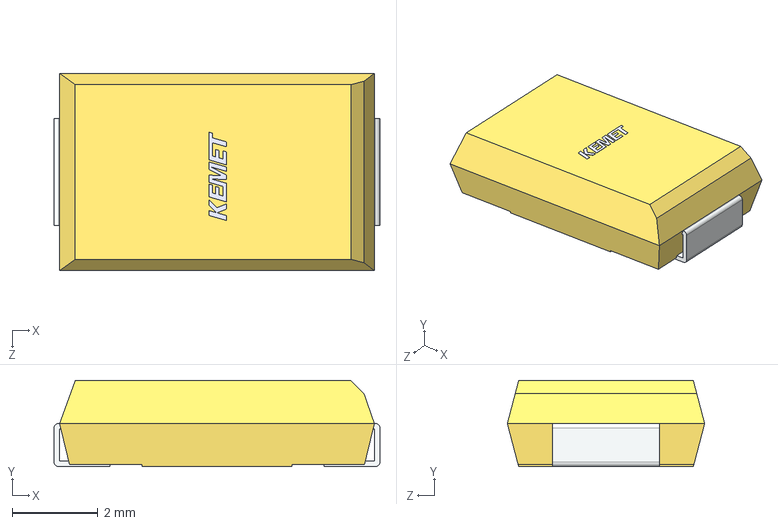
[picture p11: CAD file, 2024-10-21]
replacementLibs/T494V106K035AT/T494V106K035AT.stp
7.60 x 2.01 x 4.60 mm

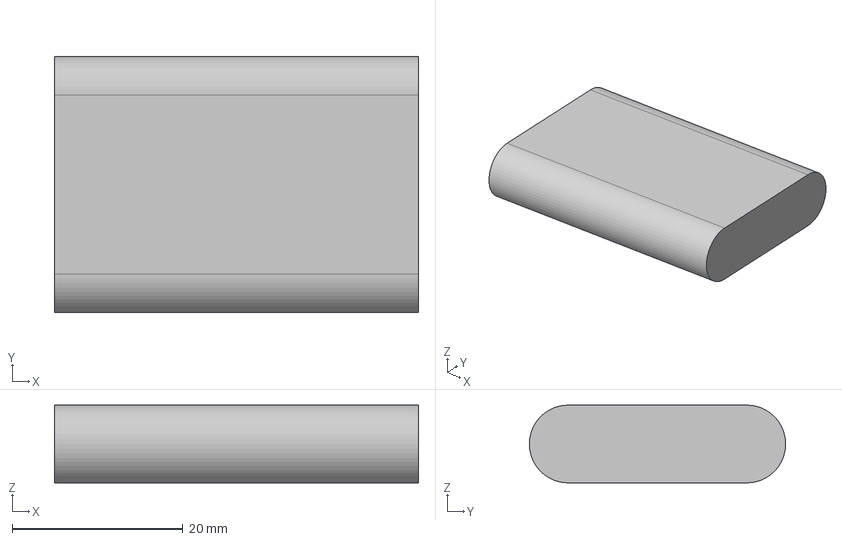
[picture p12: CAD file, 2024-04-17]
lsf-kicad-lib/3d_sources/NP-BX1.FCStd
42.6 x 30.0 x 9.10 mm

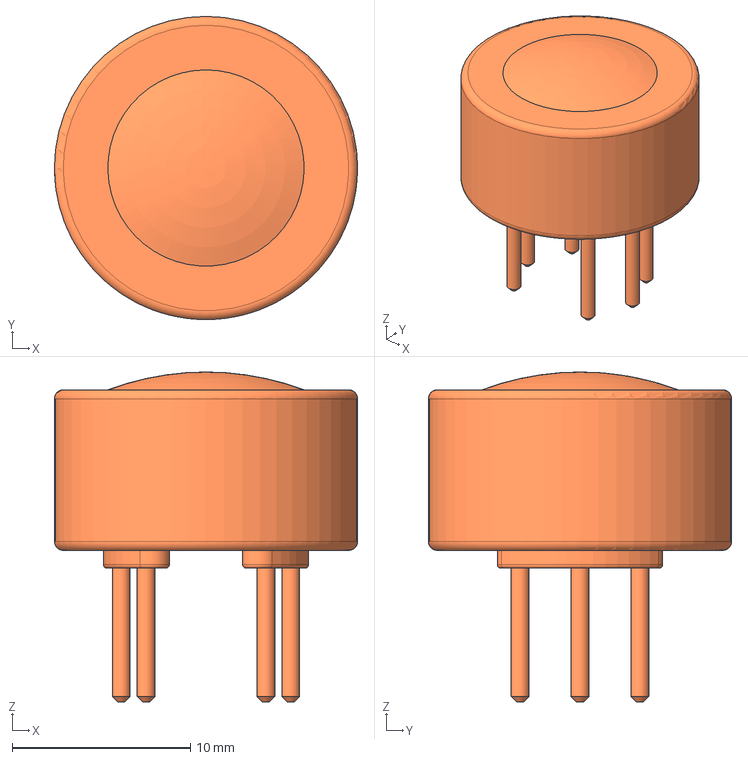
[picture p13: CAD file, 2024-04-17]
lsf-kicad-lib/3d_sources/MQ-7.FCStd
17.0 x 17.0 x 18.5 mm

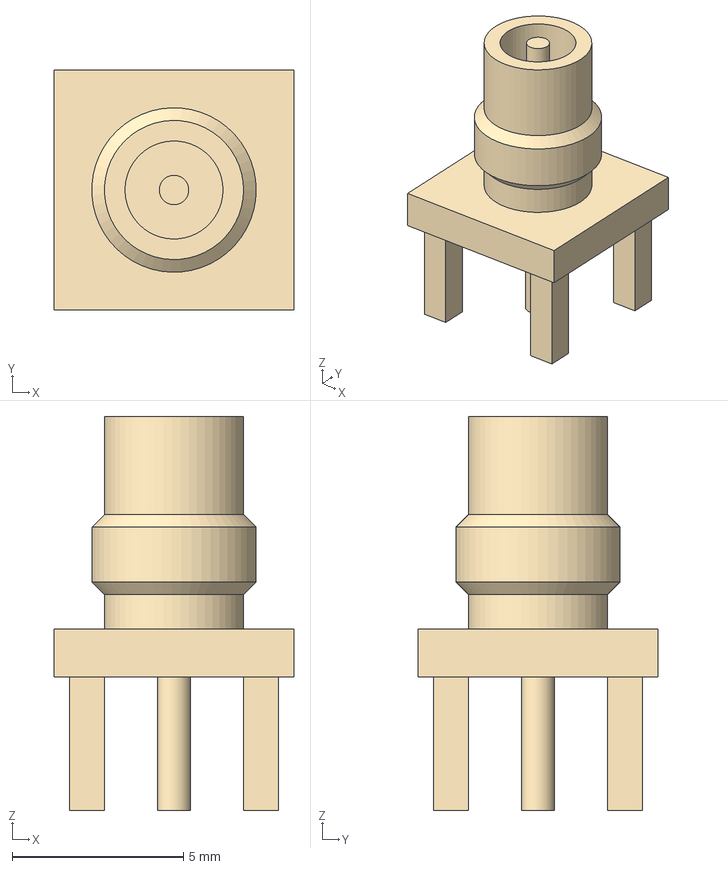
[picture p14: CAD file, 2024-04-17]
lsf-kicad-lib/3d_sources/SMC_Amphenol_152119_Vertical.FCStd
7.00 x 7.00 x 11.5 mm

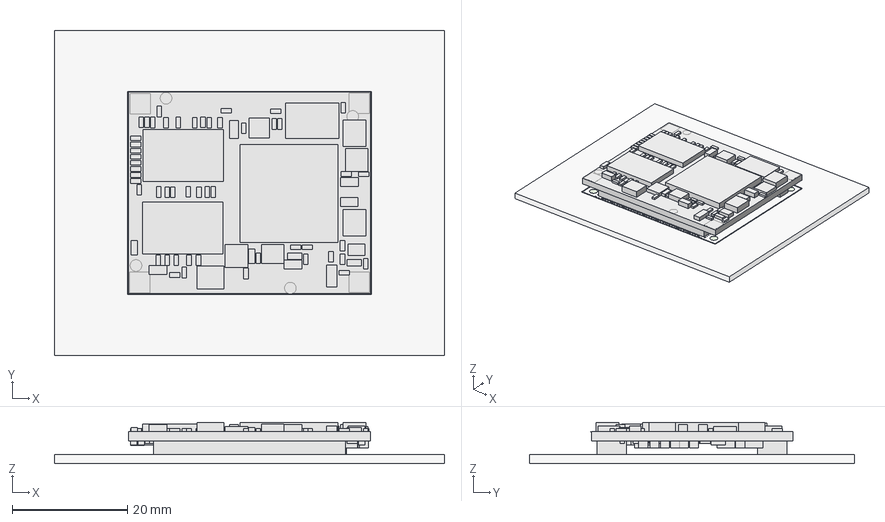
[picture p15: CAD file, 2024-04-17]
lsf-kicad-lib/3d_sources/Xilinx ZYNQ-7000 SOM.FCStd
67.7 x 56.5 x 7.15 mm
FCrtYd
FFab
FrontSilk
TopPads
PTHs
Pcb
Alinx_ZYNQ-7000_SOM_XC7Z020

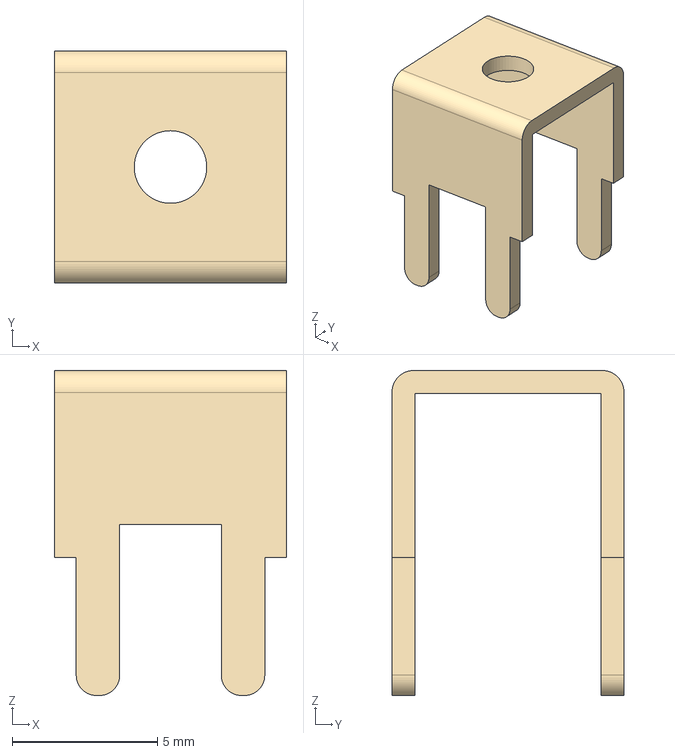
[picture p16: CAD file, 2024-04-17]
lsf-kicad-lib/3d_sources/KEYSTONE-7698.FCStd
8.00 x 8.00 x 11.2 mm

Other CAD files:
lsf-kicad-lib/3d_sources/MQ-131.FCStd
lsf-kicad-lib/3d_sources/D2F-L2-A.FCStd
lsf-kicad-lib/3d_sources/ATB2012.FCStd
lsf-kicad-lib/3d_sources/SM141K04LV.FCStd
3d_sources/ASPI-0530HI-2R2M-T2/Allegro/indpm5652x300n.psm
3d_sources/ASPI-0530HI-2R2M-T2/DEHDL/aspi_0530hi_2r2m_t2/chips/chips.prt
lsf-kicad-lib/3d/TPS63080.stp
lsf-kicad-lib/3d_sources/CONMCX001.FCStd
lsf-kicad-lib/3d_sources/D2F-L.FCStd
lsf-kicad-lib/3d_sources/D2F-L2-A1.FCStd
lsf-kicad-lib/3d_sources/DF11-10DP-2DS.FCStd
lsf-kicad-lib/3d_sources/KEYSTONE-1502-2.FCStd
lsf-kicad-lib/3d_sources/MQ-135.FCStd
lsf-kicad-lib/3d_sources/SW_SPST_SPVN110107.FCStd
replacementLibs/5040500491/5040500491.stp

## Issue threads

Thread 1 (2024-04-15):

NRST Pull-up Resistor

Basilhs-Moustakas, 2024-04-15:
This reset pin is pulled-up internally from the MCU. We could consider for the new version keeping the pull-up resistor as "Do not place" since it was causing problems in the past.

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

Closed 2024-04-15.

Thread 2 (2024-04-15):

I2C channels

Basilhs-Moustakas, 2024-04-15:
Should we also consider moving INA3221 to a different I2C channel from the sensors? I think it was causing us problems in the past having them in the same channels. You have an empty I2C channel on PD12 and PD13 pins which I think wont be a trouble routing.

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

giatats, 2024-04-15:
Added separate I2C Bus for INA (I2C4). Also added pull ups 5k.

Closed 2024-04-15.

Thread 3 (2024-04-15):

Temperature Sensor

Basilhs-Moustakas, 2024-04-15:
In the previous version we had selected the TMP117MAIDRVR temperature sensors. From the datasheet these appear to have a lower temperature range than some other versions of the same component.

I think this mostly concerns the BOM but lets make sure that the other version donot have any differences in the footprint.

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

giatats, 2024-04-15:
They are the same, we need to get either the TMP117AIDRVR or TMP117NAIDRVR.

Basilhs-Moustakas, 2024-04-29:
Generated BOM taking this into account

Closed 2024-04-29.

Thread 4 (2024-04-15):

GNSS power supply

Basilhs-Moustakas, 2024-04-15:
I understand the logic for the GNSS power supply but maybe we could also add a 0 ohm resistor between 3V3_RF and V_BCKP and also a "Donot place" 0 Ohm resistor between VCC and V_BCKP just in case we decide in the future to switch to our old configuration,

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

Closed 2024-04-15.

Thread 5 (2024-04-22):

GNSS UART lines clearance

Basilhs-Moustakas, 2024-04-22:
0.1mm clearance is kinda small. It shouldnt be a problem but it's better since we have space to increase it to 0.2 at least

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

Closed 2024-04-22.

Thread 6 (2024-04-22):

GNSS signal trackes

Basilhs-Moustakas, 2024-04-22:
Shouldnt be a problem but you can try to have RST and PPS signal perpendicular to other traces in this area to avoid cross-talk since you have space to do it

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

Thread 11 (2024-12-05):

Refine: Comments from production

maestroque, 2024-12-05:
## Assembly
- [ ] C405 Silkscreen polarity marking
- [ ] FL2 Footprint fix (RF1419D)

## PCB Production

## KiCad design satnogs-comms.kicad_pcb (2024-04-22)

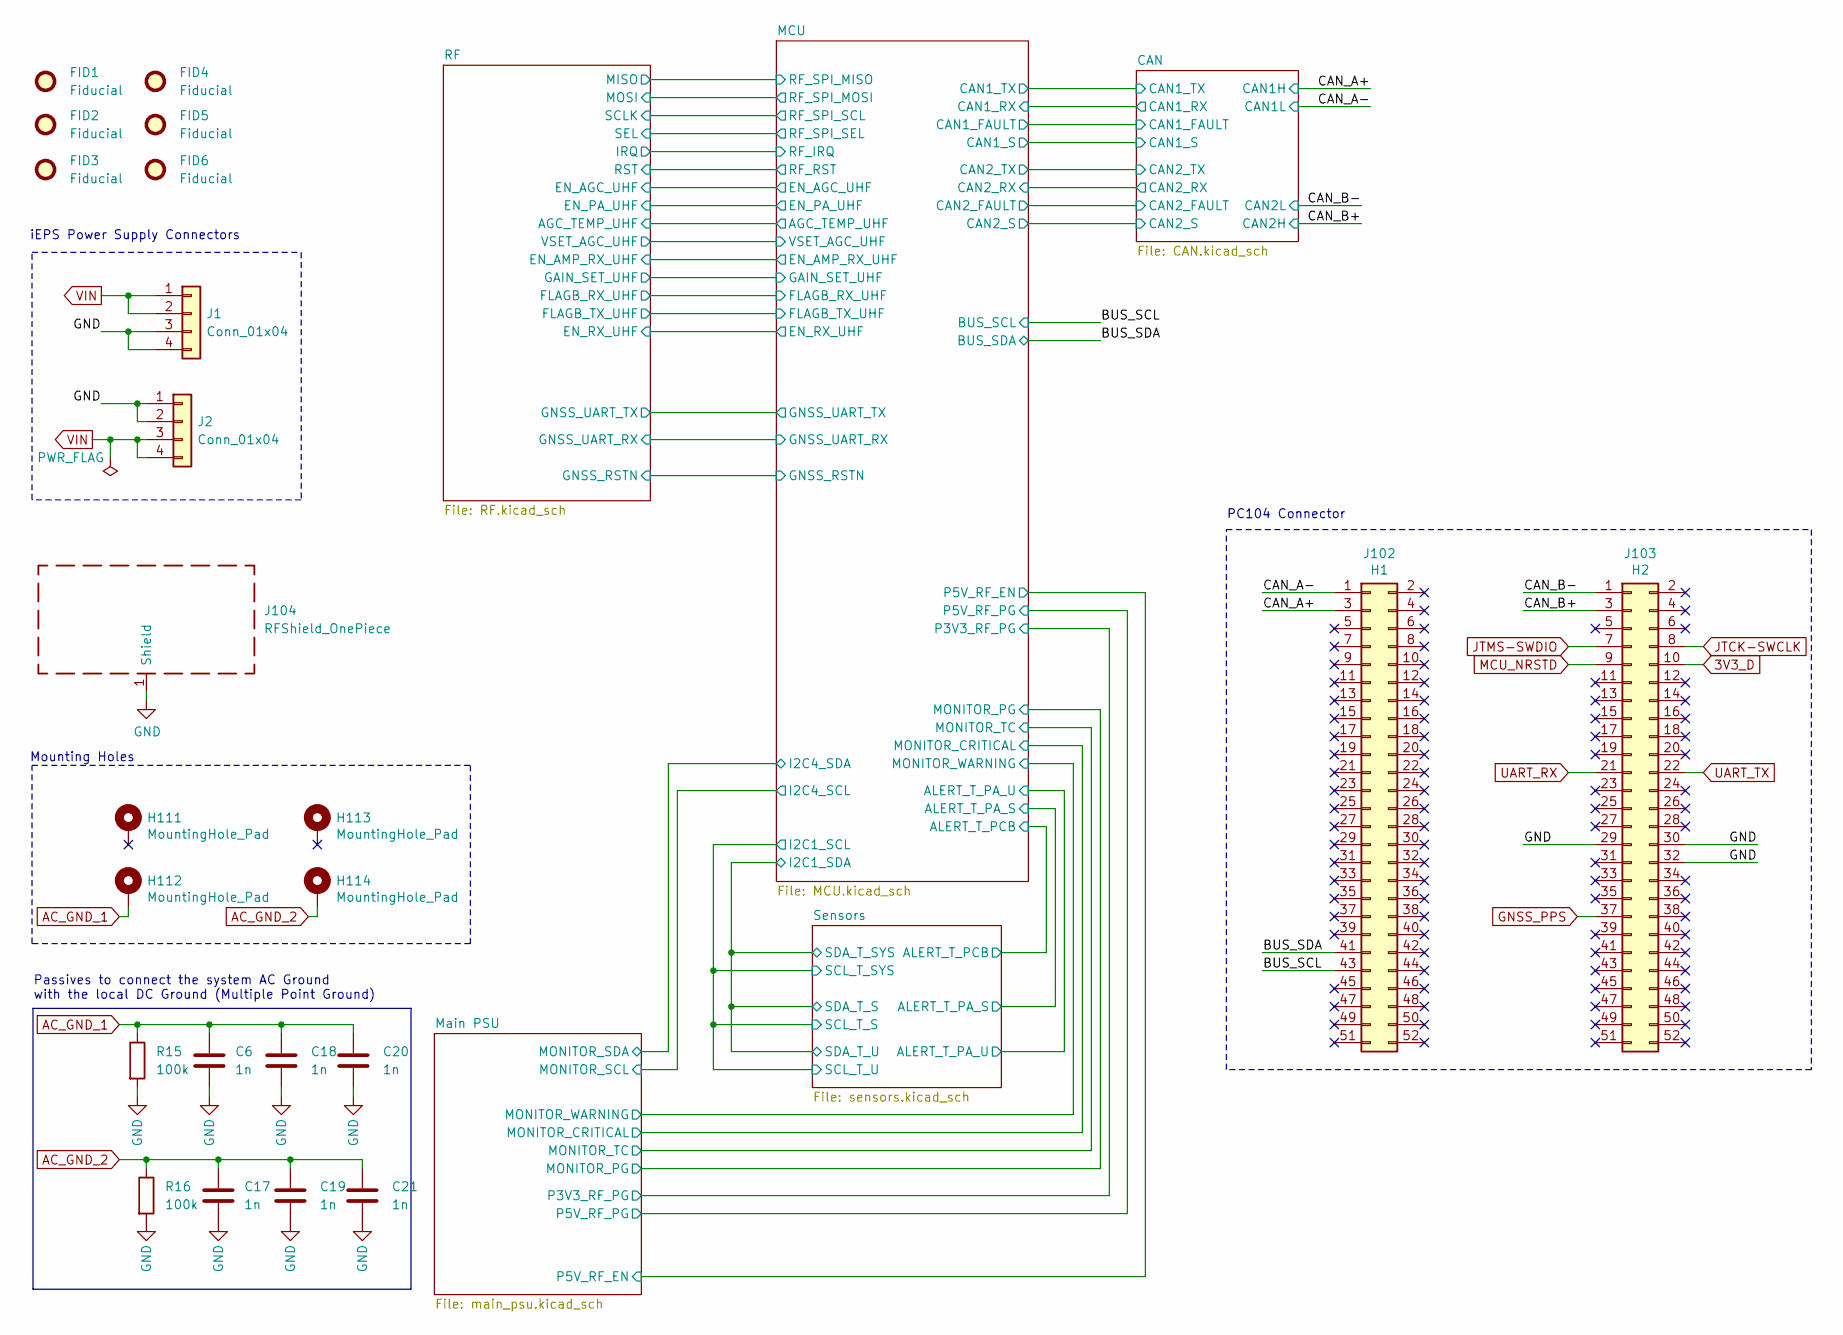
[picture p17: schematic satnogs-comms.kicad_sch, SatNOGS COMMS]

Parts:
C6, C17, C18, C19, C20, C21: 1n; C_0603_1608Metric
FID1, FID2, FID3, FID4, FID5, FID6: Fiducial; Fiducial_1mm_Mask2mm
H111, H112, H113, H114: MountingHole_Pad; MountingHole_3.2mm_M3_DIN965_Pad
J1, J2: Conn_01x04; Molex_Pico-Lock_504050-0491_1x04-1MP_P1.50mm_Horizontal
J102: Η1; ESQ-126-39-x-D; PartNumber ESQ-126-39-x-D
J103: Η2; ESQ-126-39-x-D; PartNumber ESQ-126-39-x-D
J104: RFShield_OnePiece; emi-shield-original
R15, R16: 100k; R_0603_1608Metric_Pad0.98x0.95mm_HandSolder

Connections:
/BUS_SCL: J102.43; also elsewhere on the board
/BUS_SDA: J102.41; also elsewhere on the board
/CAN_B+: J103.3; also elsewhere on the board
/CAN_B-: J103.1; also elsewhere on the board
AC_GND_2: C17.1, C19.1, C21.1, H114.1, R16.1
GNSS_PPS: J103.37; also elsewhere on the board
JTCK-SWCLK: J103.8; also elsewhere on the board
JTMS-SWDIO: J103.7; also elsewhere on the board
MCU_NRSTD: J103.9; also elsewhere on the board
UART_RX: J103.21; also elsewhere on the board
UART_TX: J103.22; also elsewhere on the board
VIN: J1.1, J1.2, J2.3, J2.4; also elsewhere on the board

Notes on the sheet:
iEPS Power Supply Connectors
Passives to connect the system AC Ground with the local DC Ground (Multiple Point Ground)
Mounting Holes
PC104 Connector

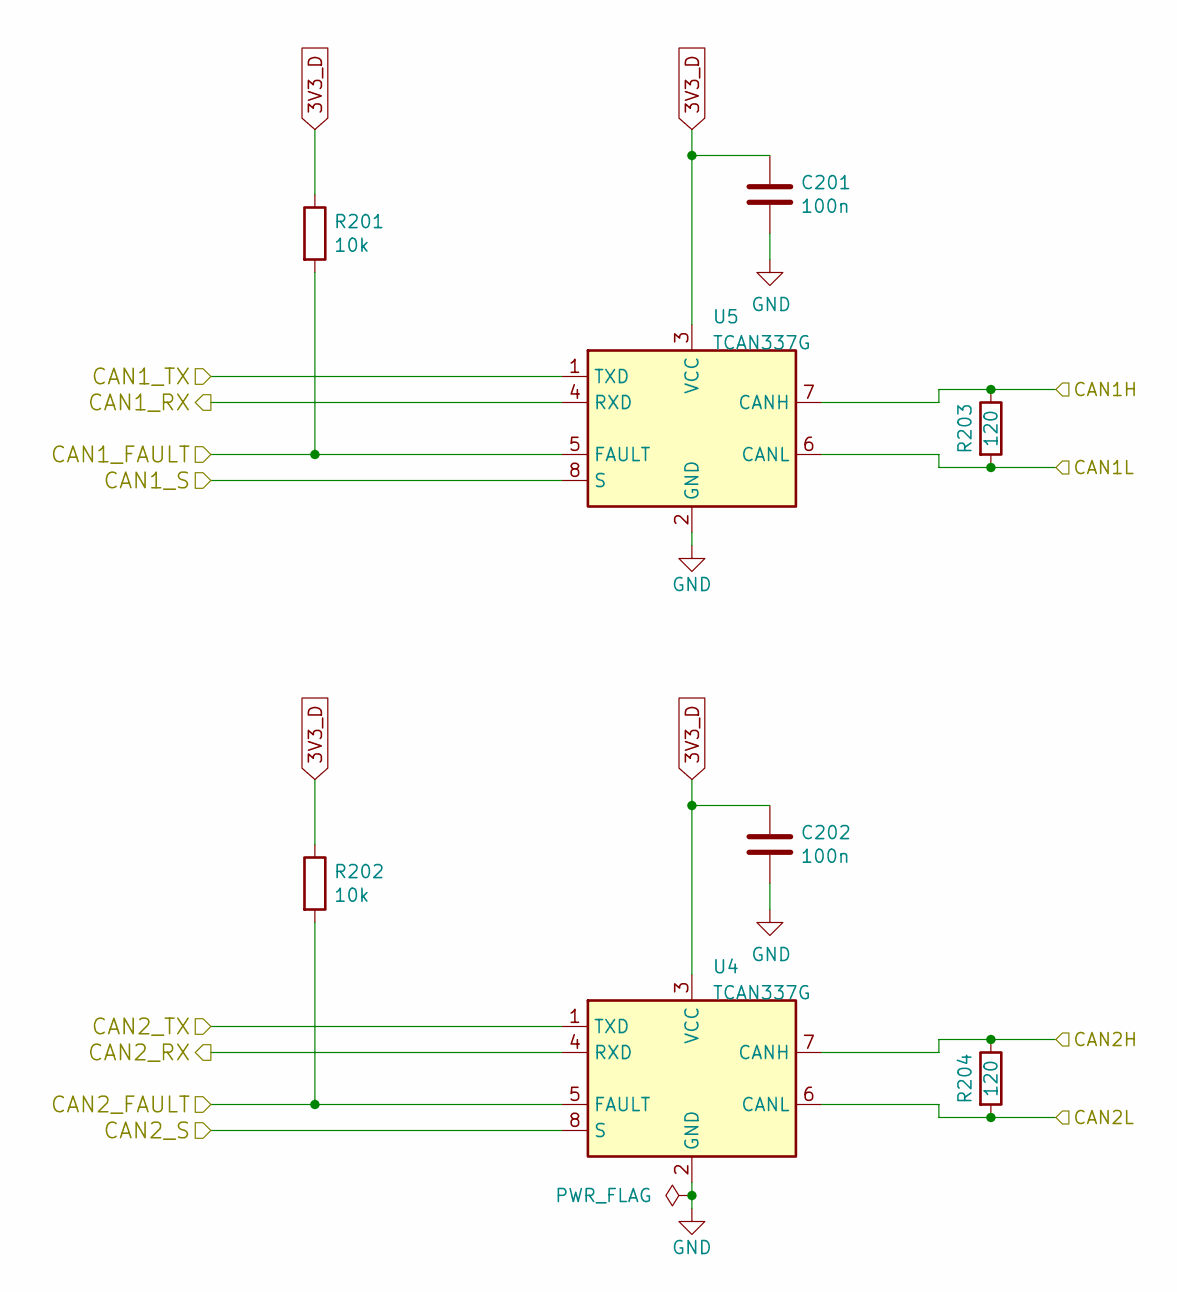
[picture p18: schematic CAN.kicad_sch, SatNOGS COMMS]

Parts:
C201, C202: 100n; C_0603_1608Metric; PartNumber C0603C104K9RACTU
R201, R202: 10k; R_0603_1608Metric_Pad0.98x0.95mm_HandSolder; PartNumber CRCW060310K0FKECC
R203, R204: 120; R_0603_1608Metric_Pad0.98x0.95mm_HandSolder; PartNumber ERJ-3EKF1200V
U4, U5: TCAN337G; SOT-23-8

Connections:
/CAN/CAN2_FAULT: R202.2, U4.5 (FAULT); also elsewhere on the board
/CAN/CAN2_RX: U4.4 (RXD); also elsewhere on the board
/CAN/CAN2_S: U4.8 (S); also elsewhere on the board
/CAN/CAN2_TX: U4.1 (TXD); also elsewhere on the board
/CAN_B+: R204.1, U4.7 (CANH); also elsewhere on the board
/CAN_B-: R204.2, U4.6 (CANL); also elsewhere on the board

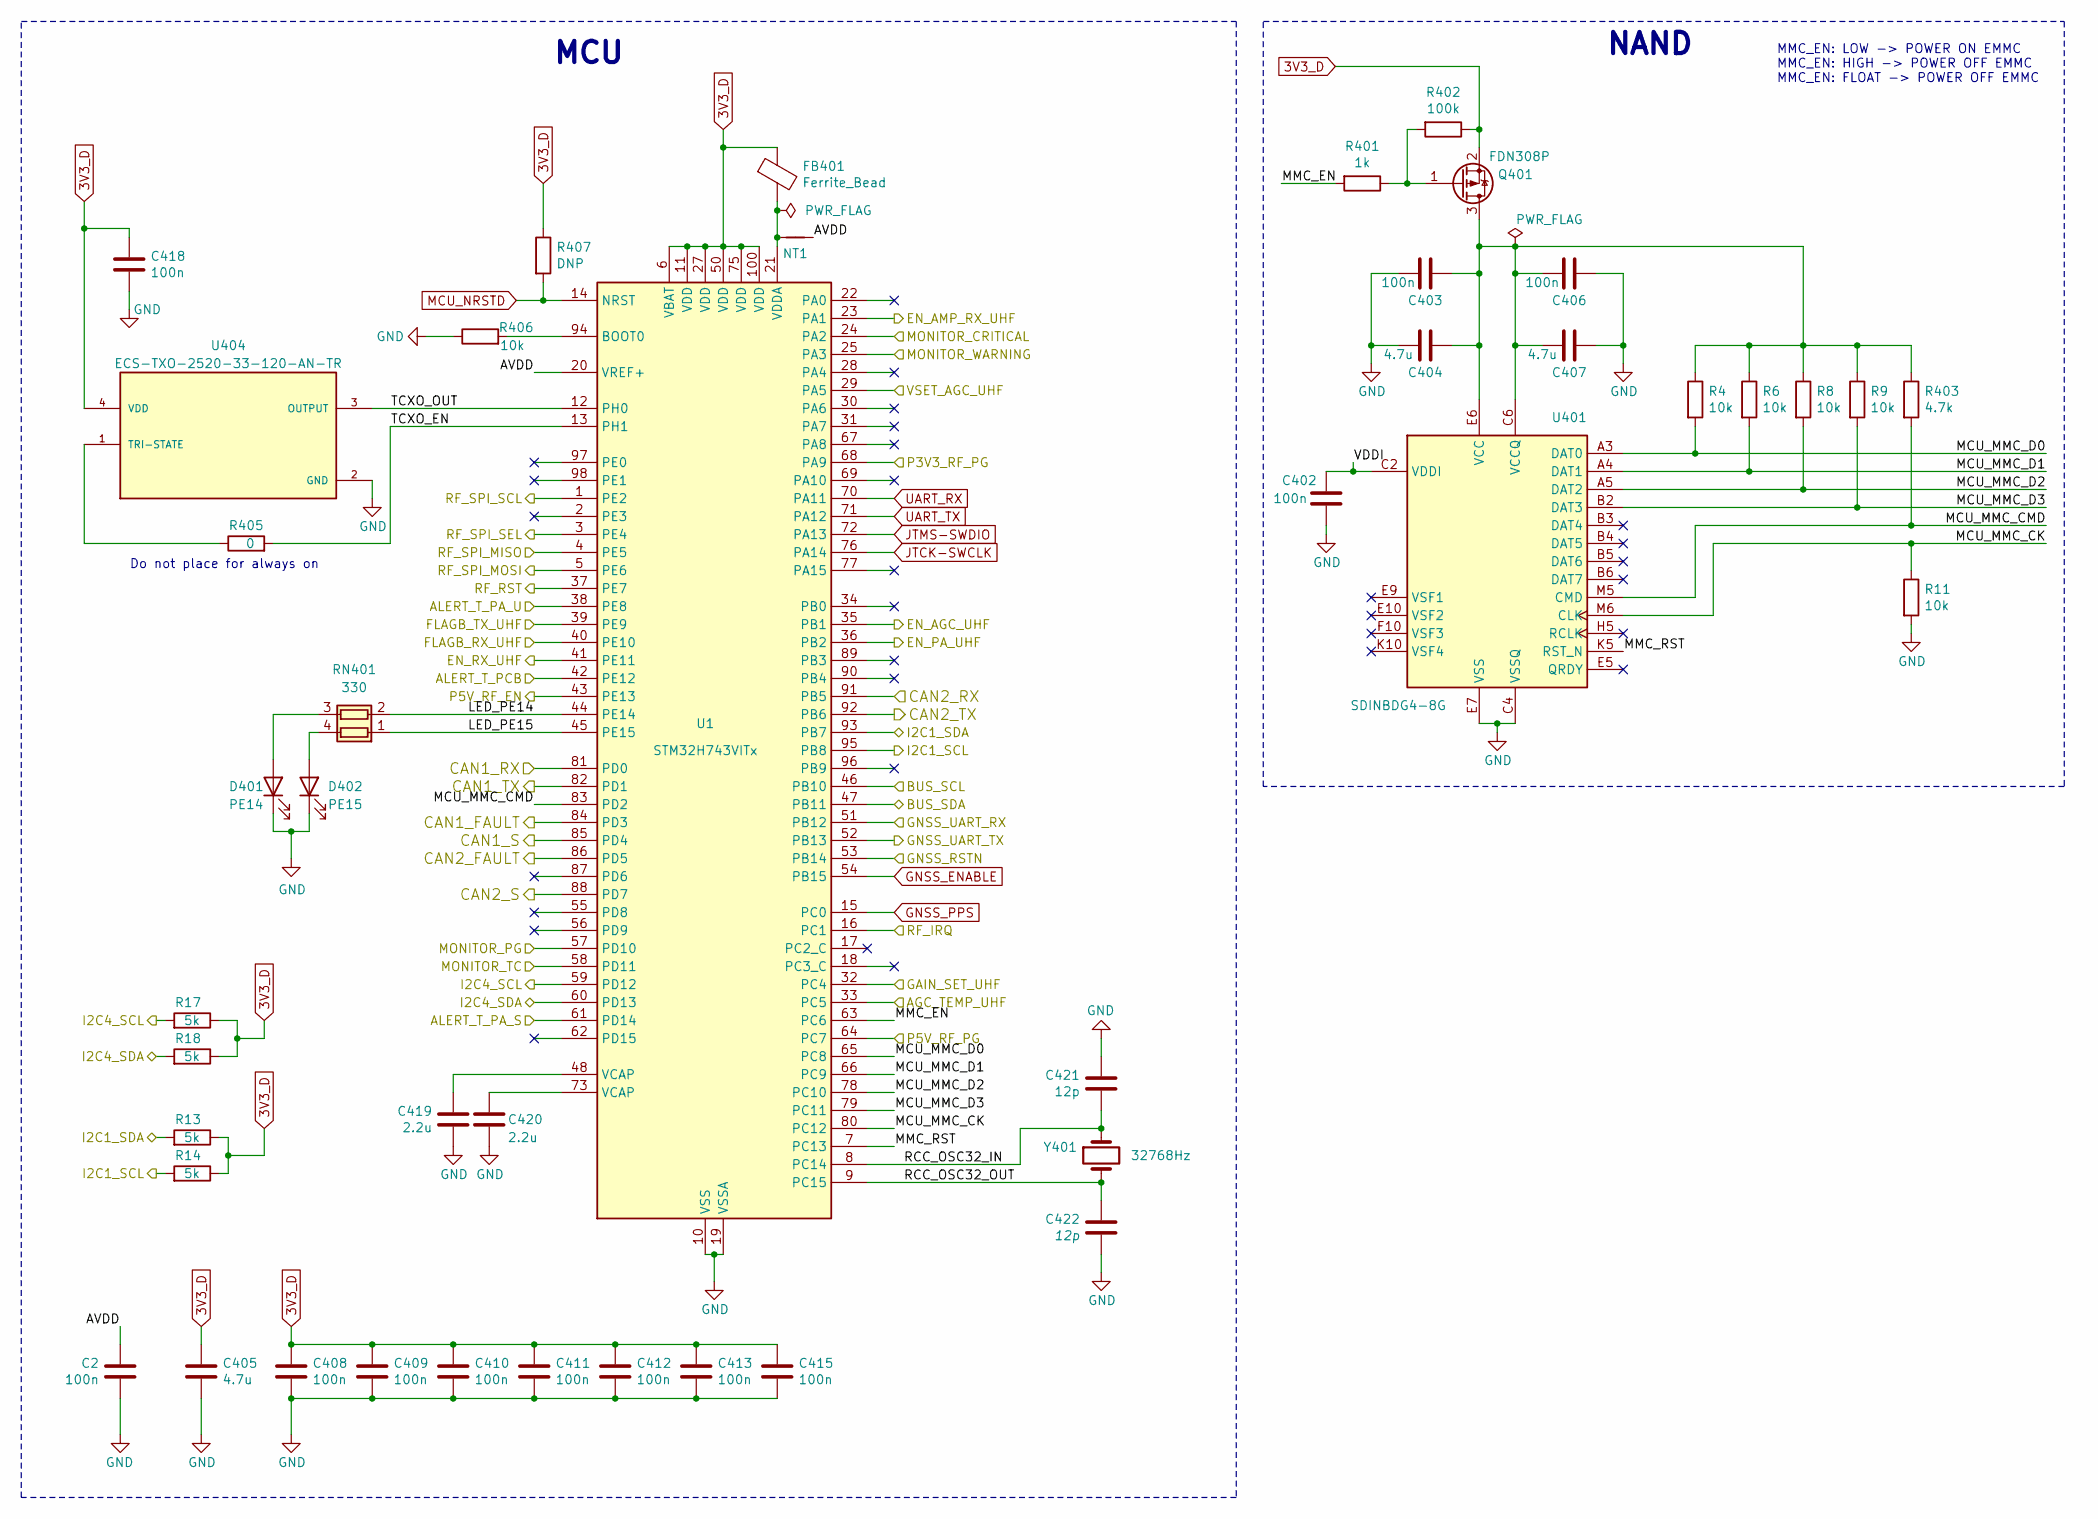
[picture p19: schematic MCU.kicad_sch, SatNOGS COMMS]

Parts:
C2, C403, C406, C408, C409, C410, C411, C412, C413, C415, C418: 100n; C_0402_1005Metric; PartNumber C0402C104K4RACTU
C402: 100n; C_0402_1005Metric; PartNumber GRM155R71A104KA01D
C404, C405, C407: 4.7u; C_1206_3216Metric; PartNumber TAJA475K016R
C419, C420: 2.2u; C_1206_3216Metric; PartNumber CC1206KKX7R7BB225
C421, C422: 12p; C_0402_1005Metric; PartNumber CBR04C120F3GAC
D401: PE14; LED_0402_1005Metric; PartNumber FHA1105P-TR
D402: PE15; LED_0402_1005Metric; PartNumber FHA1105P-TR
FB401: Ferrite_Bead; L_0603_1608Metric; PartNumber MMZ1608R601ATD25
NT1: Net-Tie_2; NetTie-2_SMD_Pad0.5mm
Q401: FDN308P; SOT-23; PartNumber FDN308P
R4, R6, R8, R9, R11, R406: 10k; R_0402_1005Metric; PartNumber CRCW040210K0FKEDC
R13, R14, R17, R18: 5k; R_0402_1005Metric; PartNumber RC0402FR-075KL
R401: 1k; R_0402_1005Metric; PartNumber CRCW04021K00FKEDC
R402: 100k; R_0402_1005Metric; PartNumber CR0402-FX-1003GLF
R403: 4.7k; R_0402_1005Metric; PartNumber CRCW040210K0FKEDC
R405: 0; R_0402_1005Metric; PartNumber RC0402JR-7D0RL
R407: DNP; R_0402_1005Metric; PartNumber CRCW040210K0FKEDC
RN401: 330; R_Array_Convex_2x0402; PartNumber EXB-24V331JX
U1: STM32H743VITx; LQFP-100_14x14mm_P0.5mm; PartNumber STM32H743VIT6
U401: SDINBDG4-8G; BGA-153_13.0mmx11.5mm_P0.5mm; PartNumber SDINBDG4-8G
U404: ECS-TXO-2520-33-120-AN-TR; OSC_ECS-TXO-2520-33-120-AN-TR; PARTREV 2017
Y401: 32768Hz; Crystal_SMD_3215-2Pin_3.2x1.5mm; PartNumber ABS07-32.768KHZ-7-T

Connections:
/BUS_SCL: U1.46 (PB10); also elsewhere on the board
/BUS_SDA: U1.47 (PB11); also elsewhere on the board
/CAN/CAN2_FAULT: U1.86 (PD5); also elsewhere on the board
/CAN/CAN2_RX: U1.91 (PB5); also elsewhere on the board
/CAN/CAN2_S: U1.88 (PD7); also elsewhere on the board
/CAN/CAN2_TX: U1.92 (PB6); also elsewhere on the board
/MCU/AGC_TEMP_UHF: U1.33 (PC5); also elsewhere on the board
/MCU/ALERT_T_PA_S: U1.61 (PD14); also elsewhere on the board
/MCU/ALERT_T_PA_U: U1.38 (PE8); also elsewhere on the board
/MCU/ALERT_T_PCB: U1.42 (PE12); also elsewhere on the board
/MCU/AVDD: C2.1, NT1.1, U1.20 (VREF+)
/MCU/EN_AGC_UHF: U1.35 (PB1); also elsewhere on the board
/MCU/EN_AMP_RX_UHF: U1.23 (PA1); also elsewhere on the board
/MCU/EN_PA_UHF: U1.36 (PB2); also elsewhere on the board
/MCU/EN_RX_UHF: U1.41 (PE11); also elsewhere on the board
/MCU/FLAGB_RX_UHF: U1.40 (PE10); also elsewhere on the board
/MCU/FLAGB_TX_UHF: U1.39 (PE9); also elsewhere on the board
/MCU/GAIN_SET_UHF: U1.32 (PC4); also elsewhere on the board
/MCU/GNSS_RSTN: U1.53 (PB14); also elsewhere on the board
/MCU/GNSS_UART_RX: U1.51 (PB12); also elsewhere on the board
/MCU/GNSS_UART_TX: U1.52 (PB13); also elsewhere on the board
/MCU/I2C1_SCL: R14.2, U1.95 (PB8); also elsewhere on the board
/MCU/I2C1_SDA: R13.2, U1.93 (PB7); also elsewhere on the board
/MCU/I2C4_SCL: R17.2, U1.59 (PD12); also elsewhere on the board
/MCU/I2C4_SDA: R18.2, U1.60 (PD13); also elsewhere on the board
/MCU/LED_PE14: RN401.2 (R2.1), U1.44 (PE14)
/MCU/LED_PE15: RN401.1 (R1.1), U1.45 (PE15)
/MCU/MCU_MMC_CK: R11.1, U1.80 (PC12), U401.M6 (CLK), U401.N7, U401.P8
/MCU/MCU_MMC_CMD: R403.2, U1.83 (PD2), U401.L12, U401.L13, U401.L14, U401.M5 (CMD)
/MCU/MCU_MMC_D0: R4.2, U1.65 (PC8), U401.A3 (DAT0)
/MCU/MCU_MMC_D1: R6.2, U1.66 (PC9), U401.A4 (DAT1)
/MCU/MCU_MMC_D2: R8.2, U1.78 (PC10), U401.A5 (DAT2)
/MCU/MCU_MMC_D3: R9.2, U1.79 (PC11), U401.A2, U401.B2 (DAT3)
/MCU/MMC_EN: R401.2, U1.63 (PC6)
/MCU/MMC_RST: U1.7 (PC13), U401.H1, U401.H2, U401.H3, U401.K5 (RST_N)
/MCU/MONITOR_CRITICAL: U1.24 (PA2); also elsewhere on the board
/MCU/MONITOR_PG: U1.57 (PD10); also elsewhere on the board
/MCU/MONITOR_TC: U1.58 (PD11); also elsewhere on the board
/MCU/MONITOR_WARNING: U1.25 (PA3); also elsewhere on the board
/MCU/P3V3_RF_PG: U1.68 (PA9); also elsewhere on the board
/MCU/P5V_RF_EN: U1.43 (PE13); also elsewhere on the board
/MCU/RCC_OSC32_IN: C421.2, U1.8 (PC14), Y401.1
/MCU/RCC_OSC32_OUT: C422.1, U1.9 (PC15), Y401.2
/MCU/RF_IRQ: U1.16 (PC1); also elsewhere on the board
/MCU/RF_RST: U1.37 (PE7); also elsewhere on the board
/MCU/RF_SPI_MISO: U1.4 (PE5); also elsewhere on the board
/MCU/RF_SPI_MOSI: U1.5 (PE6); also elsewhere on the board
/MCU/RF_SPI_SCL: U1.1 (PE2); also elsewhere on the board
/MCU/RF_SPI_SEL: U1.3 (PE4); also elsewhere on the board
/MCU/TCXO_EN: R405.2, U1.13 (PH1)
/MCU/TCXO_OUT: U1.12 (PH0), U404.3 (OUTPUT)
/MCU/VDDI: C402.1, U401.C1, U401.C2 (VDDI)
/MCU/VSET_AGC_UHF: U1.29 (PA5); also elsewhere on the board
GNSS_ENABLE: U1.54 (PB15); also elsewhere on the board
GNSS_PPS: U1.15 (PC0); also elsewhere on the board
JTCK-SWCLK: U1.76 (PA14); also elsewhere on the board
JTMS-SWDIO: U1.72 (PA13); also elsewhere on the board
MCU_NRSTD: R407.2, U1.14 (NRST); also elsewhere on the board
unnamed: C419.2, U1.48 (VCAP)
unnamed: C420.2, U1.73 (VCAP)
unnamed: D401.2 (A), RN401.3 (R2.2)
unnamed: D402.2 (A), RN401.4 (R1.2)
unnamed: C403.1, C404.1, C406.2, C407.2, Q401.3 (D), R4.1, R6.1, R8.1, R9.1, R403.1, U401.C6 (VCCQ), U401.E6 (VCC), U401.F5 (VCC), U401.J10 (VCC), U401.K9 (VCC), U401.M4 (VCCQ), U401.N4 (VCCQ), U401.P3 (VCCQ), U401.P5 (VCCQ)
unnamed: Q401.1 (G), R401.1, R402.2
unnamed: FB401.2, NT1.2, U1.21 (VDDA)
unnamed: R405.1, U404.1 (TRI-STATE)
UART_RX: U1.70 (PA11); also elsewhere on the board
UART_TX: U1.71 (PA12); also elsewhere on the board

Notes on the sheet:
Do not place for always on
MMC_EN: LOW -> POWER ON EMMC MMC_EN: HIGH -> POWER OFF EMMC MMC_EN: FLOAT -> POWER OFF EMMC
MCU
NAND

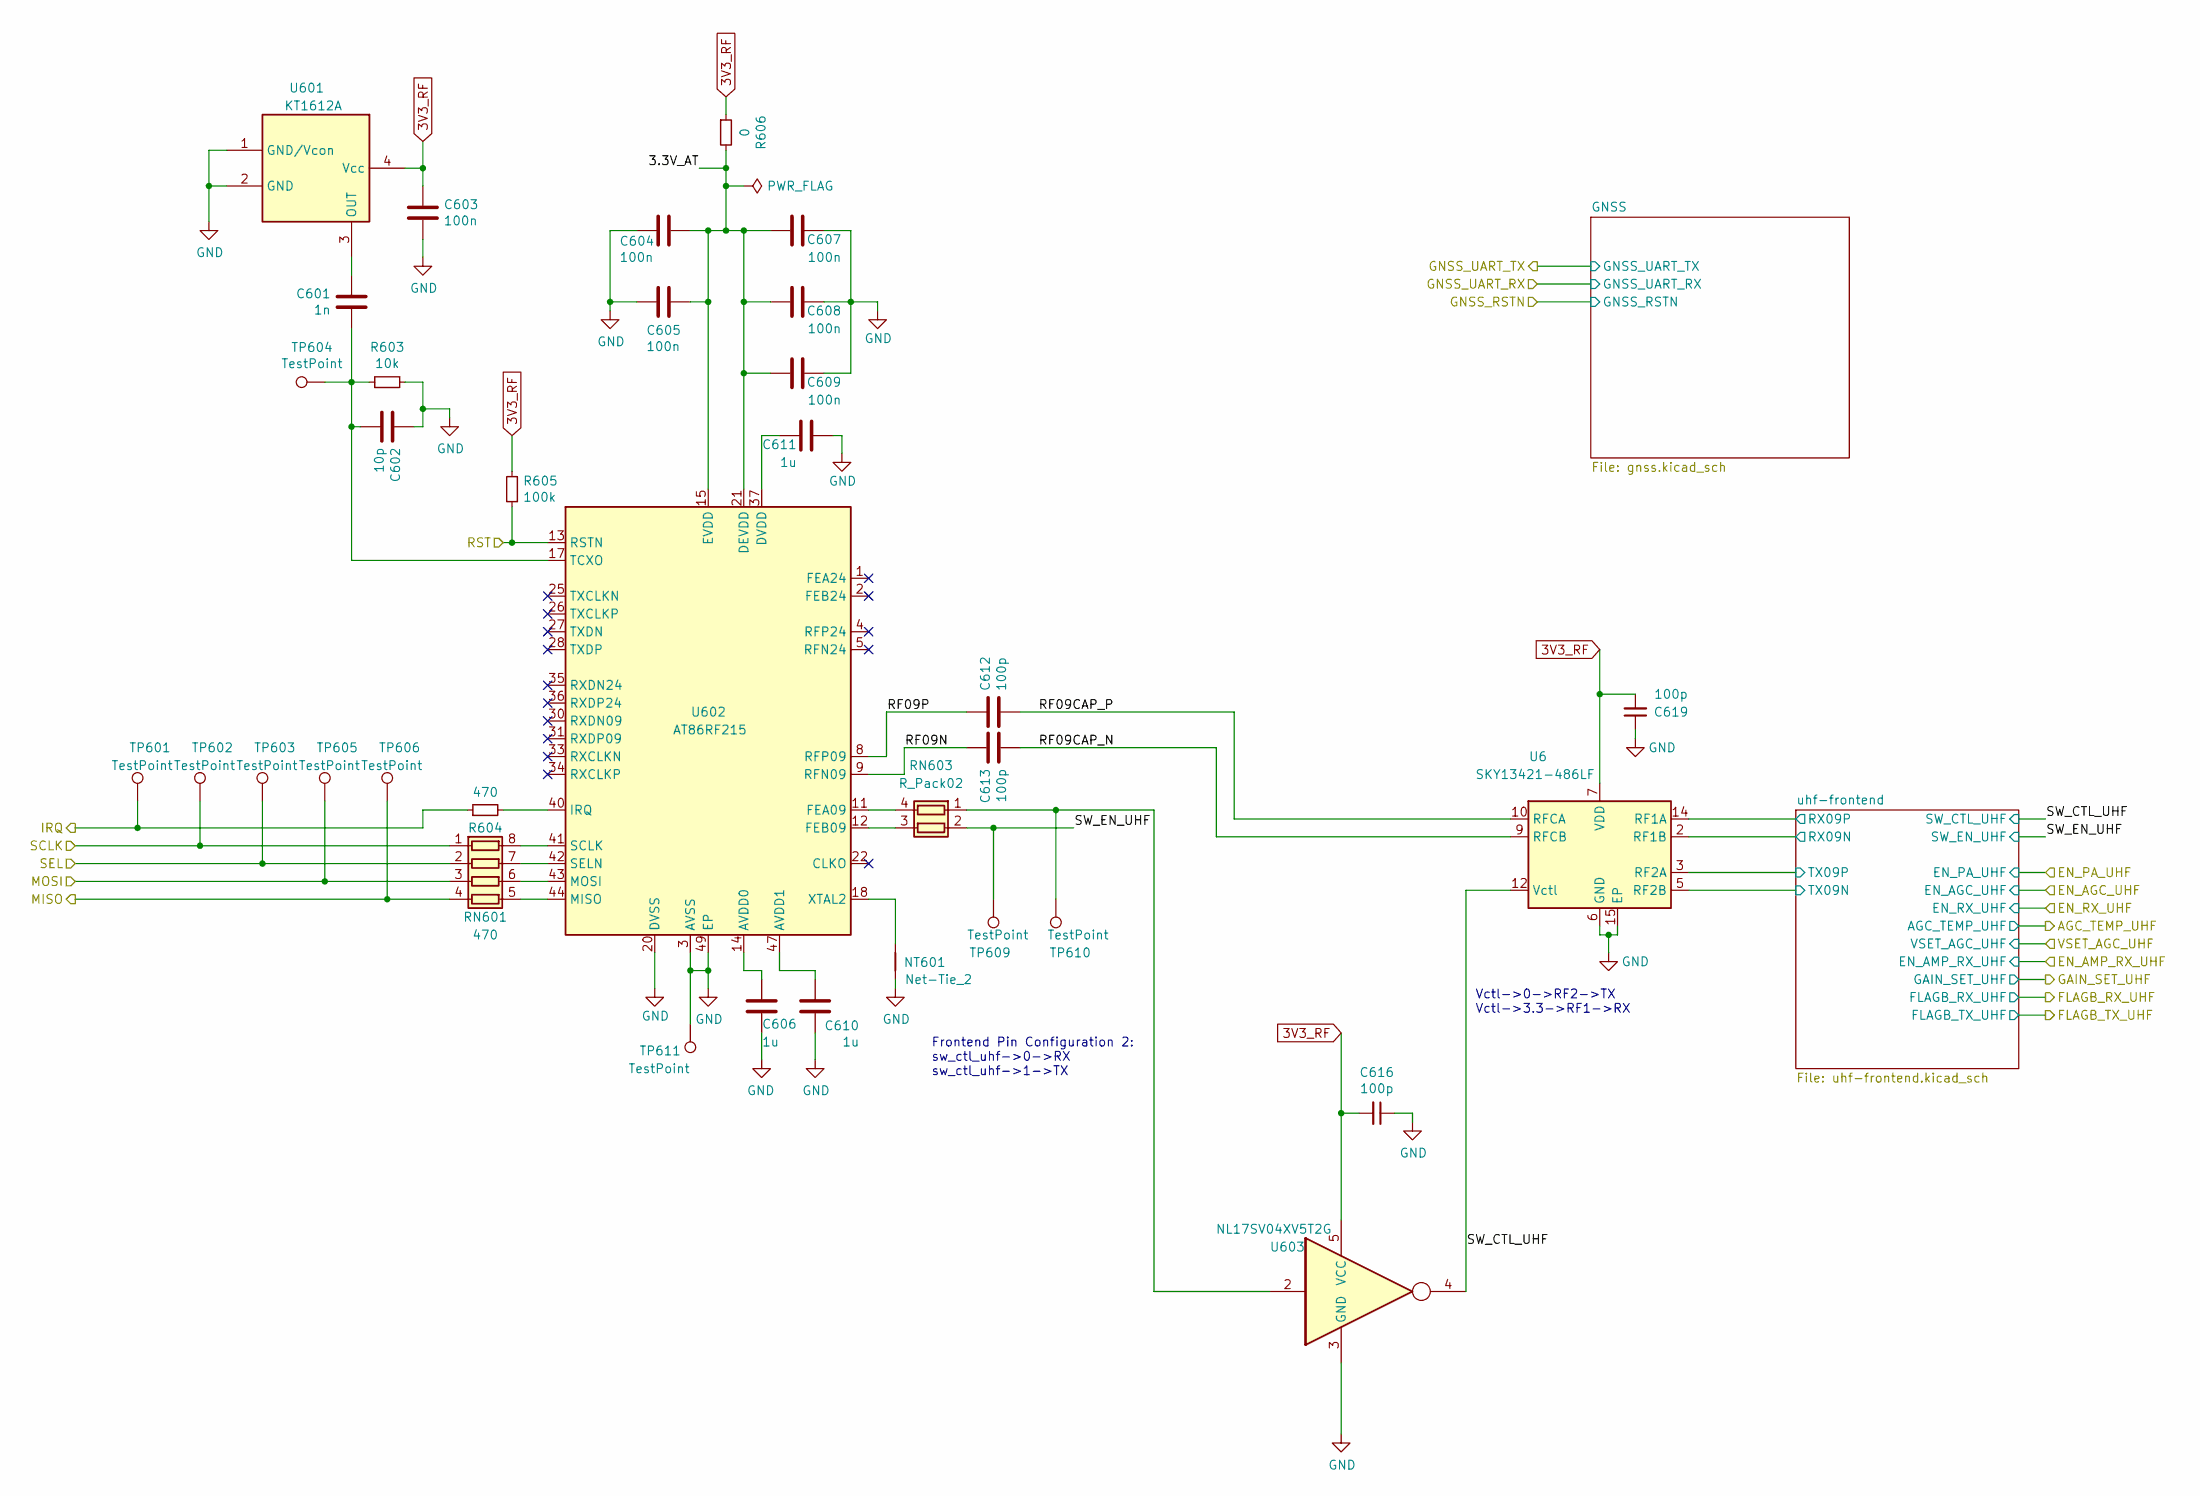
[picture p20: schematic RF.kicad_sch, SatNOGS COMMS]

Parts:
C601: 1n; C_0402_1005Metric; PartNumber C0402C102K8RACAUTO
C602: 10p; C_0402_1005Metric; PartNumber C0402C100C8GACTU
C603, C604, C605, C607, C608, C609: 100n; C_0402_1005Metric; PartNumber C0402C104K4RACTU
C606, C610, C611: 1u; C_0402_1005Metric; PartNumber C0402C105K8PAC7411
C612, C613, C616, C619: 100p; C_0402_1005Metric; PartNumber CBR04C101J3GAC
NT601: Net-Tie_2; NetTie-2_SMD_Pad0.5mm
R603: 10k; R_0402_1005Metric; PartNumber CRCW040210K0FKEDC
R604: 470; R_0402_1005Metric; PartNumber CRCW0402470RFKEDC
R605: 100k; R_0402_1005Metric; PartNumber CR0402-FX-1003GLF
R606: 0; R_0402_1005Metric; PartNumber RC0402JR-7D0RL
RN601: 470; R_Array_Convex_4x0402; PartNumber EXB-28V471JX
RN603: R_Pack02; R_Array_Convex_2x0402; PartNumber EXB-24VR000X
TP601, TP602, TP603, TP604, TP605, TP606, TP609, TP610, TP611: TestPoint; TestPoint_D0.8mm_Mask-Only
U6: SKY13421-486LF; QFN-14-1EP_1.60x1.60mm_P0.40mm_EP0.74x0.74mm
U601: KT1612A; KT1612; PartNumber KT1612A26000AAW19TBT
U602: AT86RF215; QFN-48-1EP_7x7mm_P0.5mm_EP5.6x5.6mm; PartNumber AT86RF215-ZUR
U603: NL17SV04XV5T2G; SOT-553; PartNumber NL17SV04XV5T2G

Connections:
/MCU/RF_IRQ: R604.1, TP601.1; also elsewhere on the board
/MCU/RF_RST: R605.1, U602.13 (RSTN); also elsewhere on the board
/MCU/RF_SPI_MISO: RN601.4 (R4.1), TP606.1; also elsewhere on the board
/MCU/RF_SPI_MOSI: RN601.3 (R3.1), TP605.1; also elsewhere on the board
/MCU/RF_SPI_SCL: RN601.1 (R1.1), TP602.1; also elsewhere on the board
/MCU/RF_SPI_SEL: RN601.2 (R2.1), TP603.1; also elsewhere on the board
/RF/3.3V_AT: C604.2, C605.2, C607.2, C608.2, C609.2, R606.2, U602.15 (EVDD), U602.21 (DEVDD), U602.29 (DEVDD), U602.39 (DEVDD), U602.46 (EVDD)
/RF/RF09CAP_N: C613.2, U6.9 (RFCB)
/RF/RF09CAP_P: C612.2, U6.10 (RFCA)
/RF/RF09N: C613.1, U602.9 (RFN09)
/RF/RF09P: C612.1, U602.8 (RFP09)
/RF/SW_CTL_UHF: U6.12 (Vctl), U603.4; also elsewhere on the board
/RF/SW_EN_UHF: RN603.2 (R2.1), TP609.1; also elsewhere on the board
/RF/uhf-frontend/RX09N: U6.2 (RF1B); also elsewhere on the board
/RF/uhf-frontend/RX09P: U6.14 (RF1A); also elsewhere on the board
/RF/uhf-frontend/TX09N: U6.5 (RF2B); also elsewhere on the board
/RF/uhf-frontend/TX09P: U6.3 (RF2A); also elsewhere on the board
unnamed: RN601.8 (R1.2), U602.41 (SCLK)
unnamed: RN601.7 (R2.2), U602.42 (SELN)
unnamed: RN601.6 (R3.2), U602.43 (MOSI)
unnamed: RN601.5 (R4.2), U602.44 (MISO)
unnamed: RN603.1 (R1.1), TP610.1, U603.2
unnamed: RN603.4 (R1.2), U602.11 (FEA09)
unnamed: RN603.3 (R2.2), U602.12 (FEB09)
unnamed: C601.2, U601.3 (OUT)
unnamed: C606.2, U602.14 (AVDD0)
unnamed: C610.2, U602.47 (AVDD1)
unnamed: C611.2, U602.37 (DVDD)
unnamed: R604.2, U602.40 (IRQ)
unnamed: C601.1, C602.1, R603.1, TP604.1, U602.17 (TCXO)
unnamed: NT601.1, U602.18 (XTAL2)

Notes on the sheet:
Vctl->0->RF2->TX Vctl->3.3->RF1->RX
Frontend Pin Configuration 2: sw_ctl_uhf->0->RX sw_ctl_uhf->1->TX

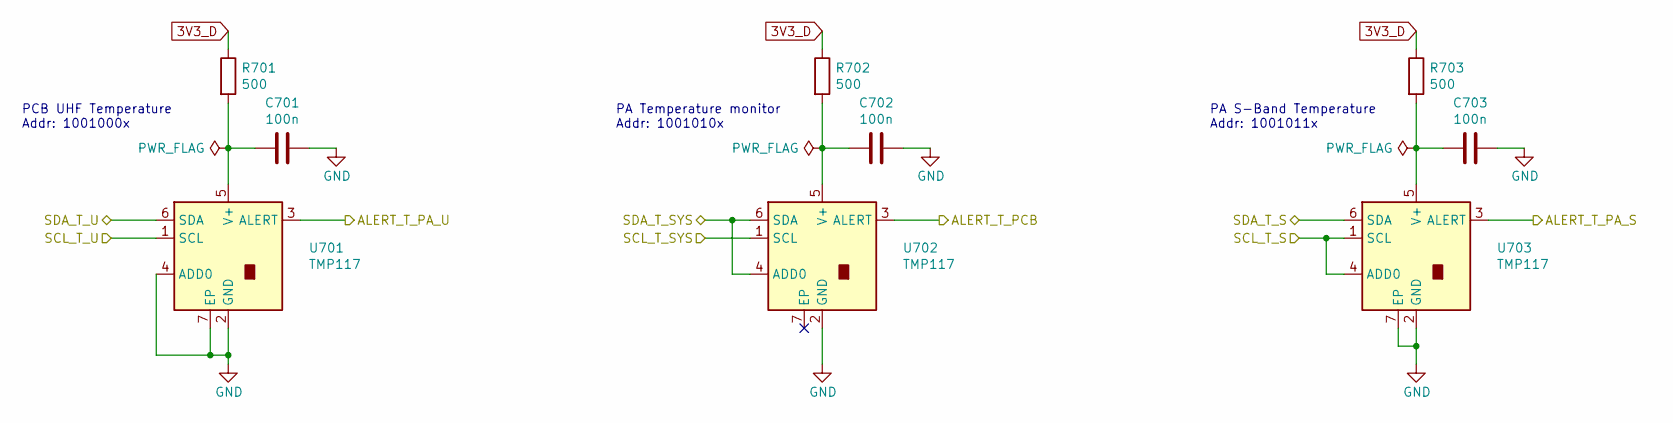
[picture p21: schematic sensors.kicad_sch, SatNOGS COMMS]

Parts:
C701, C702, C703: 100n; C_0402_1005Metric; PartNumber C0402C104K4RACTU
R701, R702, R703: 500; R_0402_1005Metric; PartNumber RR0510P-511-D
U701, U702, U703: TMP117; WSON-6-1EP_2x2mm_P0.65mm_EP1x1.6mm; PartNumber TMP117

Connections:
/MCU/ALERT_T_PA_S: U703.3 (ALERT); also elsewhere on the board
/MCU/ALERT_T_PA_U: U701.3 (ALERT); also elsewhere on the board
/MCU/ALERT_T_PCB: U702.3 (ALERT); also elsewhere on the board
/MCU/I2C1_SCL: U701.1 (SCL), U702.1 (SCL), U703.1 (SCL), U703.4 (ADD0); also elsewhere on the board
/MCU/I2C1_SDA: U701.6 (SDA), U702.4 (ADD0), U702.6 (SDA), U703.6 (SDA); also elsewhere on the board
unnamed: C701.2, R701.2, U701.5 (V+)
unnamed: C702.2, R702.2, U702.5 (V+)
unnamed: C703.2, R703.2, U703.5 (V+)

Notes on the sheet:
PA Temperature monitor Addr: 1001010x
PA S-Band Temperature Addr: 1001011x
PCB UHF Temperature Addr: 1001000x

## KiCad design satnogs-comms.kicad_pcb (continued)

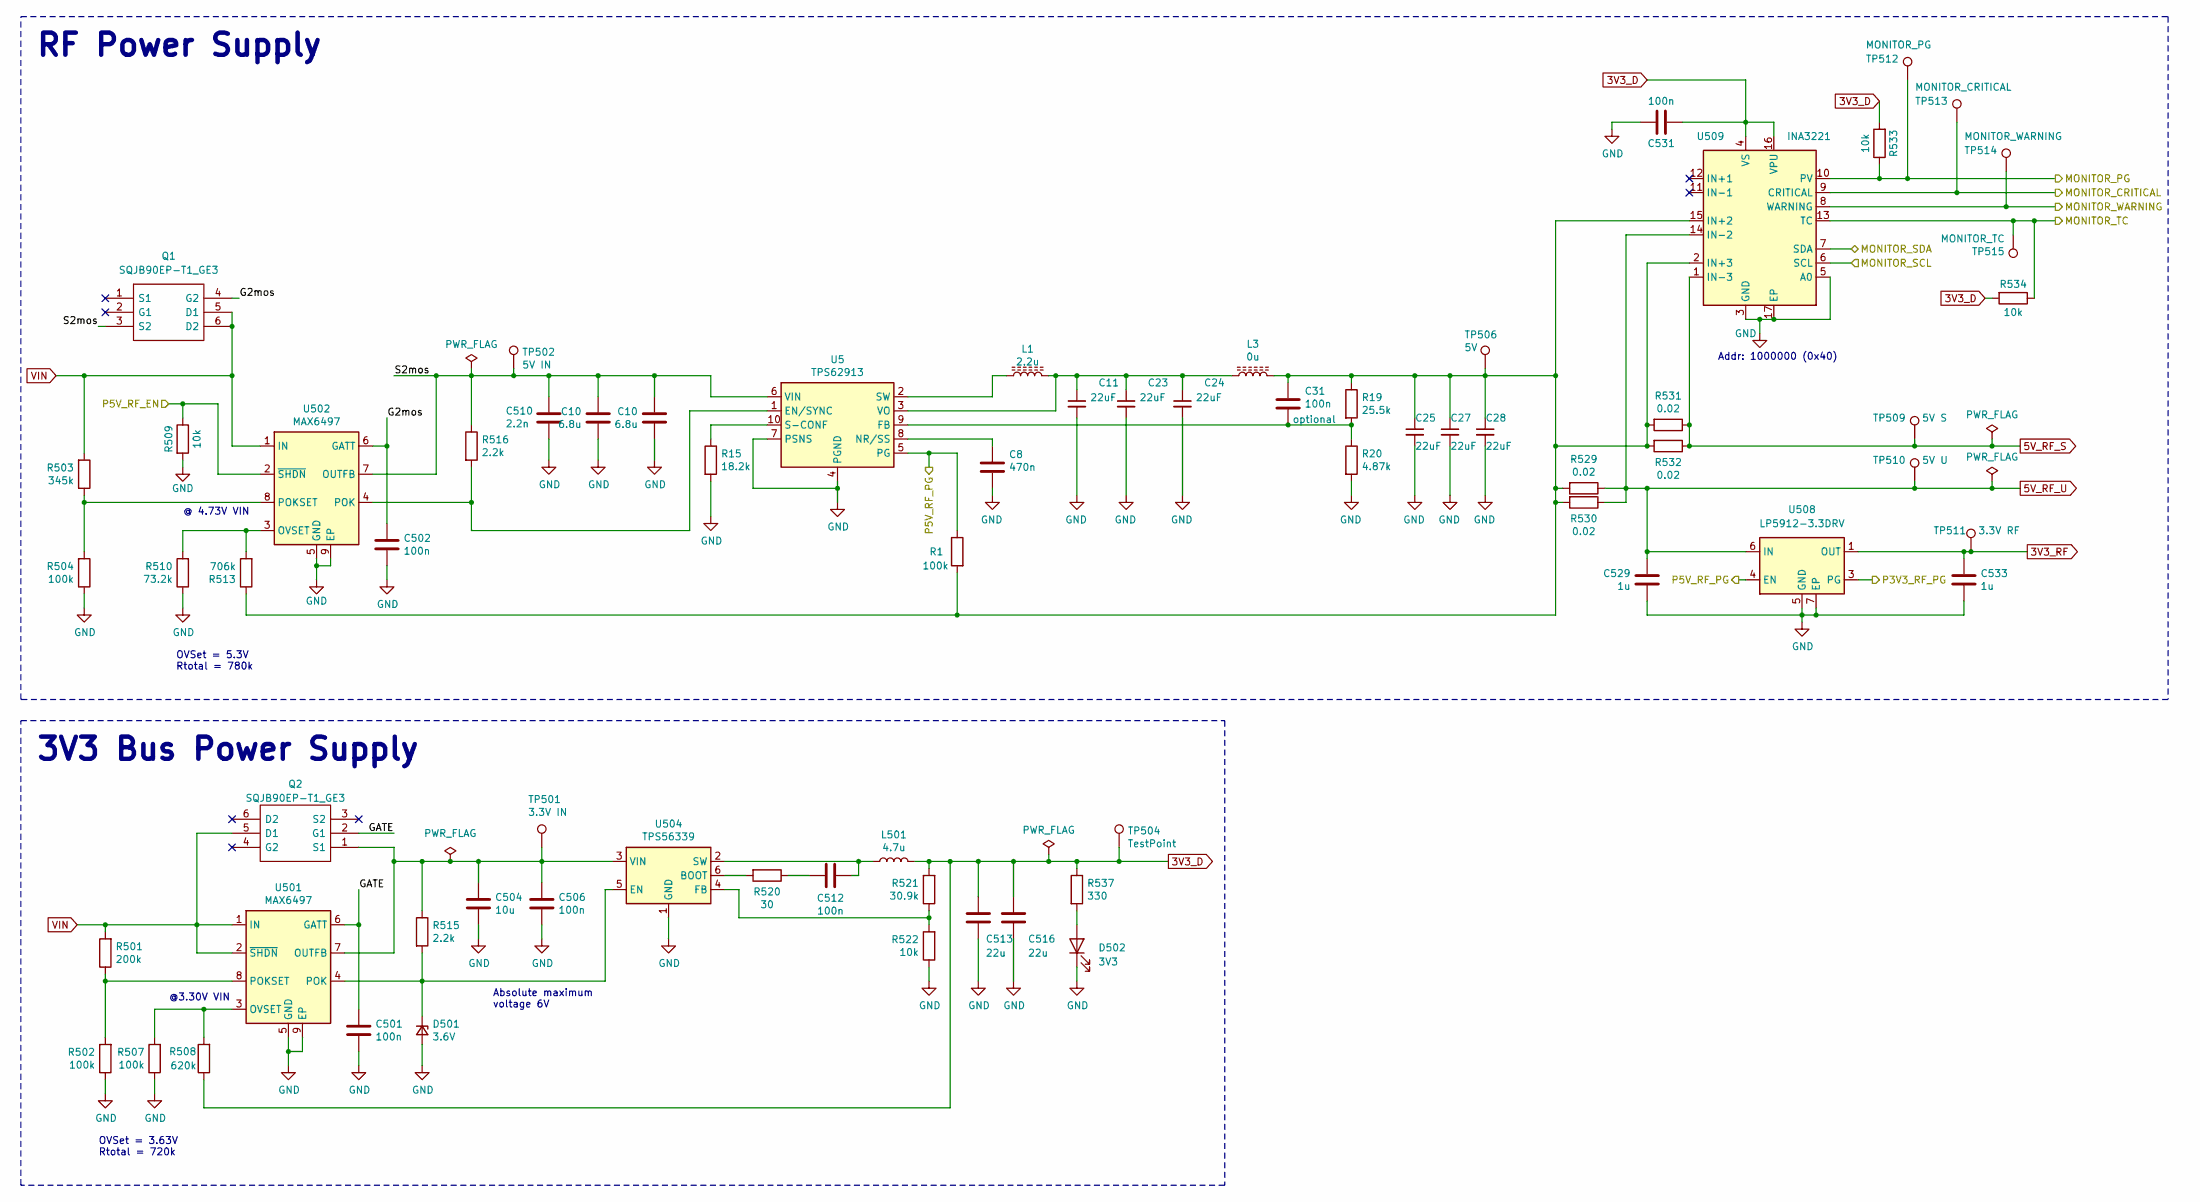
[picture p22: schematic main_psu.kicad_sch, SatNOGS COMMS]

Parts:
C8: 470n; C_0402_1005Metric; PartNumber GRM188R60J474KA01D
C10: 6.8u; C_0805_2012Metric; PartNumber C2012X5R1E685K125AC
C11, C23, C24, C25, C27, C28: 22uF; C_0805_2012Metric; PartNumber C0402C104K4RACTU
C31, C501, C502: 100n; C_0402_1005Metric; PartNumber C0402C104K4RACTU
C504: 10u; C_0805_2012Metric; PartNumber EMK212BB7106KG-T
C506, C512: 100n; C_0805_2012Metric; PartNumber C0805C104M5RACTU
C510: 2.2n; C_0402_1005Metric; PartNumber CGA2B2X7R1H222K050BA
C513, C516: 22u; C_0805_2012Metric; PartNumber GRM21BR61A226ME44L
C529, C533: 1u; C_0603_1608Metric; PartNumber EMK107B7105KA-T
C531: 100n; C_0603_1608Metric; PartNumber C0603C104K9RACTU
D501: 3.6V; D_0805_2012Metric; PartNumber BZY55B3V6 RBG
D502: 3V3; LED_0402_1005Metric; PartNumber APHHS1005LQBC/D-V
L1: 2.2u; L_Abracon_ASPI-0530HI; PartNumber ASPI-0520LR-2R2M-T2
L3: 0u; L_0805_2012Metric; PartNumber 782853200
L501: 4.7u; L_Bourns_SRN6045TA; PartNumber SRN6045-4R7Y
Q1, Q2: SQJB90EP-T1_GE3; SQJ910AEPT1_GE3; Mouser Part Number 78-SQJB90EP-T1_GE3
R1: 100k; R_0402_1005Metric; PartNumber CR0402-FX-1003GLF
R15: 18.2k; R_0402_1005Metric; PartNumber CRCW040218K2FKED
R19: 25.5k; R_0402_1005Metric; PartNumber CRCW040225K5FKED
R20: 4.87k; R_0402_1005Metric; PartNumber CRCW04024K87FKEDC
R501: 200k; R_0603_1608Metric; PartNumber CRCW0603620KFKEAC
R502, R504: 100k; R_0603_1608Metric; PartNumber RT0603FRE071KL
R503: 345k; R_0603_1608Metric; PartNumber RN731JTTD3443F100
R507: 100k; R_0603_1608Metric; PartNumber RT0603FRE0791RL
R508: 620k; R_0603_1608Metric; PartNumber CRCW0603523KFKEA
R509, R533, R534: 10k; R_0402_1005Metric; PartNumber CRCW040210K0FKEDC
R510: 73.2k; R_0603_1608Metric; PartNumber RT0603FRE0773K2L
R513: 706k; R_0603_1608Metric; PartNumber RN73H1JTTD7063D100
R515, R516: 2.2k; R_0603_1608Metric; PartNumber CR0603-JW-222ELF
R520: 30; R_0603_1608Metric; PartNumber RC0603FR-0730RL
R521: 30.9k; R_0603_1608Metric; PartNumber ERJ-U03F3092V
R522: 10k; R_0603_1608Metric; PartNumber CRCW060310K0FKECC
R529, R530, R531, R532: 0.02; R_0805_2012Metric; PartNumber RCWH080520L0FMEA
R537: 330; R_0402_1005Metric; PartNumber ERA-2AED331X
TP501: 3.3V IN; TestPoint_D0.8mm_Mask-Only
TP502: 5V IN; TestPoint_D0.8mm_Mask-Only
TP504: TestPoint; TestPoint_D0.8mm_Mask-Only
TP506: 5V; TestPoint_D0.8mm_Mask-Only
TP509: 5V S; TestPoint_D0.8mm_Mask-Only
TP510: 5V U; TestPoint_D0.8mm_Mask-Only
TP511: 3.3V RF; TestPoint_D0.8mm_Mask-Only
TP512: MONITOR_PG; TestPoint_D0.8mm_Mask-Only
TP513: MONITOR_CRITICAL; TestPoint_D0.8mm_Mask-Only
TP514: MONITOR_WARNING; TestPoint_D0.8mm_Mask-Only
TP515: MONITOR_TC; TestPoint_D0.8mm_Mask-Only
U5: TPS62913; Texas_VQFN-10-HR_2x2_Pitch0.5mm; PartNumber TPS62913
U501, U502: MAX6497; Maxim_T833-2_TDFN-8-1EP_3x3mm_P0.65mm_EP1.5x2.3mm; PartNumber MAX6497ATA+T
U504: TPS56339; SOT-23-6; PartNumber TPS56339DDCR
U508: LP5912-3.3DRV; WSON-6-1EP_2x2mm_P0.65mm_EP1x1.6mm_ThermalVias; PartNumber LP5912-3.3DRV
U509: INA3221; Texas_RGV_S-PVQFN-N16_EP2.1x2.1mm; PartNumber INA3221

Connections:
5V_RF_S: R531.1, R532.1, TP509.1, U509.1 (IN-3)
5V_RF_U: C529.1, R529.1, R530.1, TP510.1, U508.6 (IN), U509.14 (IN-2); also elsewhere on the board
/MCU/I2C4_SCL: U509.6 (SCL); also elsewhere on the board
/MCU/I2C4_SDA: U509.7 (SDA); also elsewhere on the board
/MCU/MONITOR_CRITICAL: TP513.1, U509.9 (CRITICAL); also elsewhere on the board
/MCU/MONITOR_PG: R533.1, TP512.1, U509.10 (PV); also elsewhere on the board
/MCU/MONITOR_TC: R534.1, TP515.1, U509.13 (TC); also elsewhere on the board
/MCU/MONITOR_WARNING: TP514.1, U509.8 (WARNING); also elsewhere on the board
/MCU/P3V3_RF_PG: U508.3 (PG); also elsewhere on the board
/MCU/P5V_RF_EN: R509.1, U502.2 (~SHDN); also elsewhere on the board
/Main PSU/G2mos: C502.1, Q1.4 (G2), U502.6 (GATT)
/Main PSU/GATE: C501.1, Q2.2 (G1), U501.6 (GATT)
unnamed: C512.2, R520.1
unnamed: D501.1 (K), R515.2, U501.4 (POK), U504.5 (EN)
unnamed: D502.2 (A), R537.2
unnamed: C504.1, C506.1, Q2.1 (S1), R515.1, TP501.1, U501.7 (OUTFB), U504.3 (VIN)
unnamed: R507.2, R508.2, U501.3 (OVSET)
unnamed: R501.1, R502.2, U501.8 (POKSET)
unnamed: R510.2, R513.2, U502.3 (OVSET)
unnamed: R503.1, R504.2, U502.8 (POKSET)
unnamed: R520.2, U504.6 (BOOT)
unnamed: R521.1, R522.2, U504.4 (FB)
unnamed: C512.1, L501.1, U504.2 (SW)
unnamed 140: C25.1, C27.1, C28.1, C31.1, L3.2, R1.2, R513.1, R529.2, R530.2, R531.2, R532.2, TP506.1, U509.2 (IN+3), U509.15 (IN+2); also elsewhere on the board
VIN: Q1.5 (D1), Q1.6 (D2), Q1.7, Q1.8, Q1.9, Q1.10, Q2.5 (D1), Q2.8, Q2.9, R501.2, R503.2, U501.1 (IN), U501.2 (~SHDN), U502.1 (IN); also elsewhere on the board

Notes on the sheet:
RF Power Supply
OVSet = 3.63V Rtotal = 720k
@ 4.73V VIN
@3.30V VIN
OVSet = 5.3V Rtotal = 780k
Absolute maximum voltage 6V
Addr: 1000000 (0x40)
3V3 Bus Power Supply

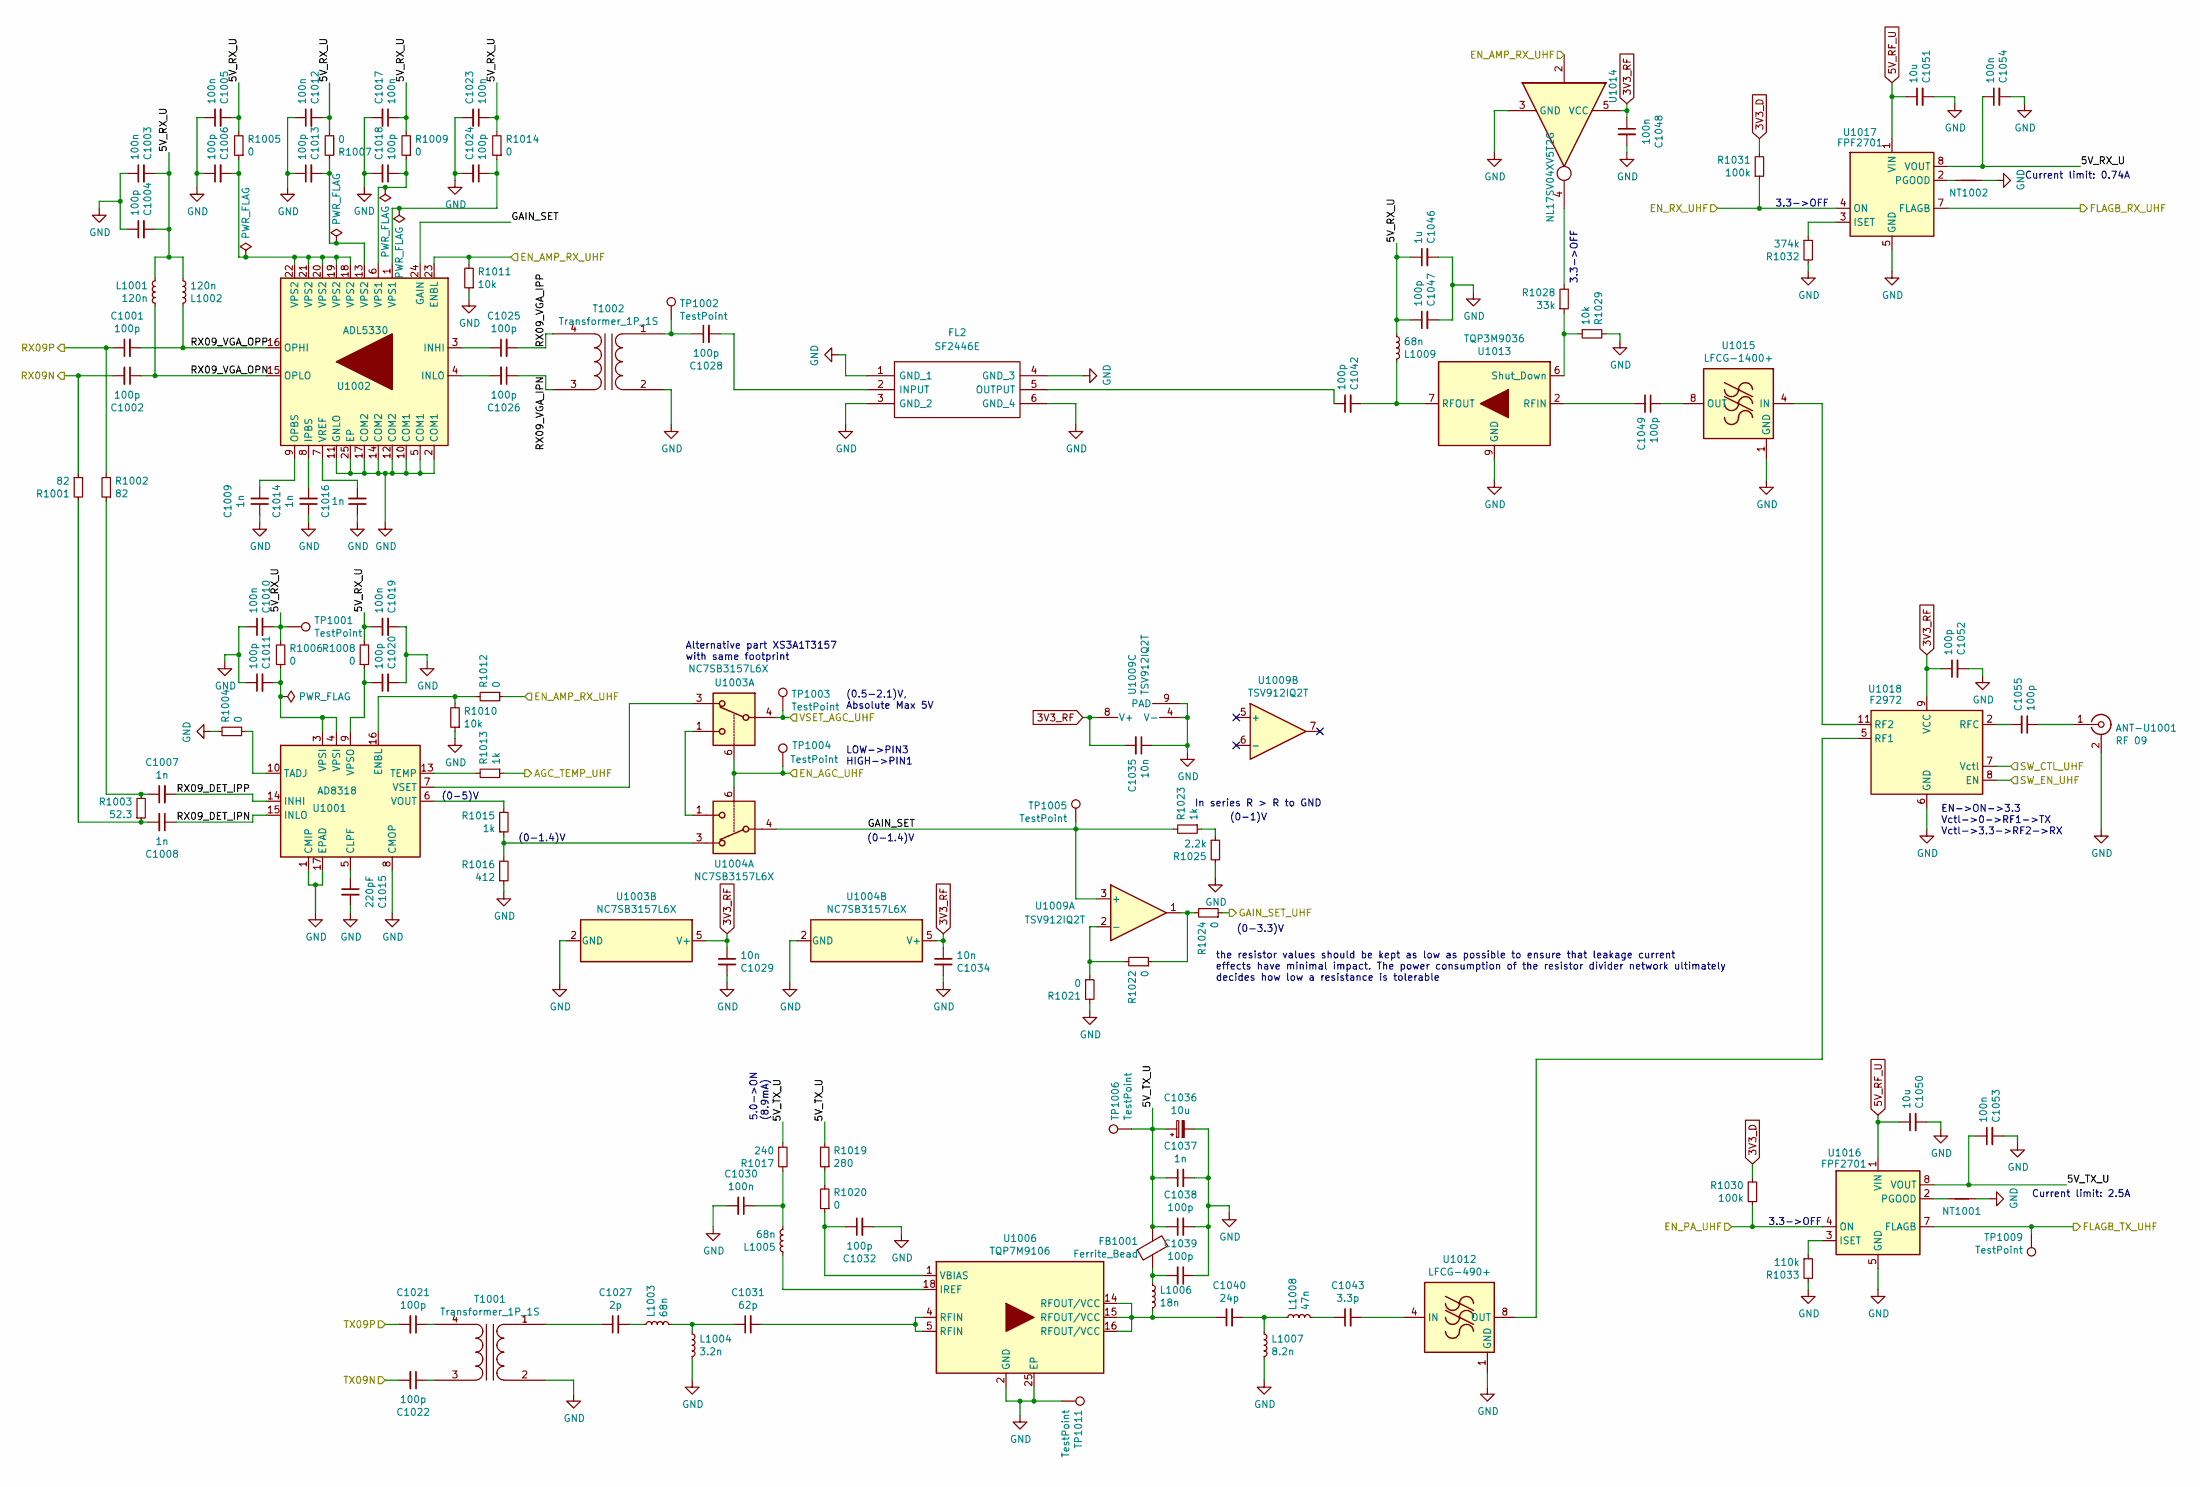
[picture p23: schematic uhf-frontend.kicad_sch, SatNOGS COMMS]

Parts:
ANT-U1001: RF 09; MMCX_Molex_73415-0961_Horizontal_1.6mm-PCB; PartNumber 73415-0961
C1001, C1002, C1004, C1006, C1011, C1013, C1018, C1020, C1021, C1022, C1024, C1025, C1026, C1028, C1032, C1038, C1039, C1042, C1047, C1049, C1052, C1055: 100p; C_0402_1005Metric; PartNumber CBR04C101J3GAC
C1003, C1005, C1010, C1012, C1017, C1019, C1023, C1048, C1053, C1054: 100n; C_0402_1005Metric; PartNumber C0402C104K4RACTU
C1007, C1008, C1009, C1014, C1016: 1n; C_0402_1005Metric; PartNumber C0402C102K8RACAUTO
C1015: 220pF; C_0603_1608Metric; PartNumber GRM033R71E221KA01D
C1027: 2p; C_0402_1005Metric; PartNumber GJM1555C1H2R0WB01D
C1029, C1034, C1035: 10n; C_0402_1005Metric; PartNumber C0402C103K9RACTU
C1030: 100n; C_0402_1005Metric; PartNumber CGA2B3X5R1H104K050BB
C1031: 62p; C_0402_1005Metric; PartNumber 04025A620FAT2A
C1036: 10u; T495C; PartNumber T495C106K035ATE400
C1037: 1n; C_0402_1005Metric; PartNumber C0402C102K5GECAUTO7411
C1040: 24p; C_0402_1005Metric; PartNumber 04025U240FAT2A
C1043: 3.3p; C_0402_1005Metric; PartNumber GJM1555C1H3R3WB01D
C1046: 1u; C_0402_1005Metric; PartNumber C0402C105K8PAC7411
C1050, C1051: 10u; C_0805_2012Metric; PartNumber EMK212BB7106KG-T
FB1001: Ferrite_Bead; L_0603_1608Metric; PartNumber BLM18KG331SN1D
FL2: SF2446E; Manufacturer_Part_Number SF2446E
L1001, L1002: 120n; L_0402_1005Metric; PartNumber LQG15WZR12J02D
L1003: 68n; L_0402_1005Metric; PartNumber MHQ1005P68NGTD25
L1004: 3.2n; L_0402_1005Metric; PartNumber LQG15WZ3N2B02D
L1005, L1009: 68n; L_0402_1005Metric; PartNumber 0402DC-68NXJRW
L1006: 18n; L_0402_1005Metric; PartNumber LQW15AN18NJ80D
L1007: 8.2n; L_0402_1005Metric; PartNumber MHQ1005P8N2GT000
L1008: 47n; L_0402_1005Metric; PartNumber AISC-0402-47NG-T
NT1001, NT1002: Net-Tie_2; NetTie-2_SMD_Pad0.5mm
R1001, R1002: 82; R_0402_1005Metric; PartNumber ERA-2AEB820X
R1003: 52.3; R_0402_1005Metric; PartNumber RG1005P-52R3-B-T5
R1004, R1005, R1006, R1007, R1008, R1009, R1012, R1014, R1020, R1021, R1022, R1024: 0; R_0402_1005Metric; PartNumber RC0402JR-7D0RL
R1010, R1011, R1029: 10k; R_0402_1005Metric; PartNumber CRCW040210K0FKEDC
R1013, R1015, R1023: 1k; R_0402_1005Metric; PartNumber CRCW04021K00FKEDC
R1016: 412; R_0402_1005Metric; PartNumber CRCW0402412RFKED
R1017: 240; R_0402_1005Metric; PartNumber CRCW0402240RFKEDC
R1019: 280; R_0402_1005Metric; PartNumber RC0402FR-07280RL
R1025: 2.2k; R_0402_1005Metric; PartNumber CRCW04022K20JNEDC
R1028: 33k; R_0402_1005Metric; PartNumber CR0402-FX-3302GLF
R1030, R1031: 100k; R_0402_1005Metric; PartNumber CR0402-FX-1003GLF
R1032: 374k; R_0402_1005Metric; PartNumber CRCW0402374KFKED
R1033: 110k; R_0402_1005Metric; PartNumber CRCW0402110KFKED
T1001, T1002: Transformer_1P_1S; ATB2012; PartNumber ATB2012-50011-T000
TP1001, TP1002, TP1003, TP1004, TP1005, TP1006, TP1009: TestPoint; TestPoint_D0.8mm_Mask-Only
TP1011: TestPoint; TestPoint_Keystone_5015_Micro-Minature; PartNumber 5015
U1001: AD8318; QFN-16-1EP_4x4mm_P0.65mm_EP2.1x2.1mm_ThermalVias; PartNumber AD8318ACPZ-REEL7
U1002: ADL5330; LFCSP-24-1EP_4x4mm_P0.5mm_EP2.3x2.3mm_ThermalVias; PartNumber ADL5330ACPZ-REEL7
U1003, U1004: NC7SB3157L6X; Fairchild_MicroPak-6_1.0x1.45mm_P0.5mm; PartNumber XS3A1T3157GSH
U1006: TQP7M9106; QFN-24-1EP_4x4mm_P0.5mm_EP2.7x2.7mm_ThermalVias; PartNumber TQP7M9106
U1009: TSV912IQ2T; DFN-8-1EP_2x2mm_P0.5mm_EP1.05x1.75mm; PartNumber TSV912IQ2T
U1012: LFCG-490+; GE0805C-2; PartNumber LFCG-490+
U1013: TQP3M9036; DFN-8-1EP_2x2mm_P0.5mm_EP0.7x1.6mm; PartNumber TQP3M9036
U1014: NL17SV04XV5T2G; SOT-553; PartNumber NL17SV04XV5T2G
U1015: LFCG-1400+; GE0805C-2; PartNumber LFCG-1400+
U1016, U1017: FPF2701; MLP-8; PartNumber FPF2701MPX
U1018: F2972; IDT_NEG-12-1EP_2x2mm_P0.5mm_EP1.1x1.1mm_ThermalVias; PartNumber F2972NEGK

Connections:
5V_RF_U: C1050.1, C1051.1, U1016.1 (VIN), U1017.1 (VIN); also elsewhere on the board
/MCU/AGC_TEMP_UHF: R1013.1; also elsewhere on the board
/MCU/EN_AGC_UHF: TP1004.1, U1003.6, U1004.6; also elsewhere on the board
/MCU/EN_AMP_RX_UHF: R1011.2, R1012.1, U1002.23 (ENBL), U1014.2; also elsewhere on the board
/MCU/EN_PA_UHF: R1030.1, U1016.4 (ON); also elsewhere on the board
/MCU/EN_RX_UHF: R1031.1, U1017.4 (ON); also elsewhere on the board
/MCU/FLAGB_RX_UHF: U1017.7 (FLAGB); also elsewhere on the board
/MCU/FLAGB_TX_UHF: TP1009.1, U1016.7 (FLAGB); also elsewhere on the board
/MCU/GAIN_SET_UHF: R1024.1; also elsewhere on the board
/MCU/VSET_AGC_UHF: TP1003.1, U1003.4; also elsewhere on the board
/RF/SW_CTL_UHF: U1018.7 (Vctl); also elsewhere on the board
/RF/SW_EN_UHF: U1018.8 (EN); also elsewhere on the board
/RF/uhf-frontend/5V_RX_U: C1003.2, C1004.2, C1005.2, C1010.2, C1012.2, C1017.1, C1019.1, C1023.1, C1046.1, C1047.1, C1054.1, L1001.1, L1002.2, L1009.2, R1005.2, R1006.2, R1007.1, R1008.2, R1009.2, R1014.2, TP1001.1, U1017.8 (VOUT)
/RF/uhf-frontend/5V_TX_U: C1036.1, C1037.1, C1038.1, C1053.1, FB1001.2, R1017.1, R1019.2, TP1006.1, U1016.8 (VOUT)
/RF/uhf-frontend/GAIN_SET: R1023.2, TP1005.1, U1002.24 (GAIN), U1004.4, U1009.3 (+)
/RF/uhf-frontend/RX09N: C1002.2, R1001.1; also elsewhere on the board
/RF/uhf-frontend/RX09P: C1001.1, R1002.2; also elsewhere on the board
/RF/uhf-frontend/RX09_DET_IPN: C1008.1, U1001.15 (INLO)
/RF/uhf-frontend/RX09_DET_IPP: C1007.2, U1001.14 (INHI)
/RF/uhf-frontend/RX09_VGA_IPN: C1026.1, T1002.3 (SA)
/RF/uhf-frontend/RX09_VGA_IPP: C1025.2, T1002.4 (SB)
/RF/uhf-frontend/RX09_VGA_OPN: C1002.1, L1001.2, U1002.15 (OPLO)
/RF/uhf-frontend/RX09_VGA_OPP: C1001.2, L1002.1, U1002.16 (OPHI)
/RF/uhf-frontend/TX09N: C1022.2; also elsewhere on the board
/RF/uhf-frontend/TX09P: C1021.2; also elsewhere on the board
unnamed: ANT-U1001.1 (In), C1055.1
unnamed: C1006.2, R1005.1, U1002.18 (VPS2), U1002.19 (VPS2), U1002.20 (VPS2), U1002.21 (VPS2), U1002.22 (VPS2)
unnamed: C1007.1, R1002.1, R1003.2
unnamed: C1008.2, R1001.2, R1003.1
unnamed: C1011.2, R1006.1, U1001.3 (VPSI), U1001.4 (VPSI)
unnamed: C1013.2, R1007.2, U1002.13 (VPS2)
unnamed: C1018.1, R1009.1, U1002.6 (VPS1)
unnamed: C1024.1, R1014.1, U1002.1 (VPS1)
unnamed: C1027.2, L1003.1
unnamed: C1030.1, L1005.2, R1017.2
unnamed: C1031.1, L1003.2, L1004.1
unnamed: C1031.2, U1006.4 (RFIN), U1006.5 (RFIN)
unnamed: C1039.2, FB1001.1, L1006.1
unnamed: C1040.1, L1006.2, U1006.14 (RFOUT/VCC), U1006.15 (RFOUT/VCC), U1006.16 (RFOUT/VCC)
unnamed: C1040.2, L1007.1, L1008.1
unnamed: C1043.1, L1008.2
unnamed: C1028.2, FL2.2 (INPUT)
unnamed: C1042.1, FL2.5 (OUTPUT)
unnamed: R1015.1, R1016.2, U1004.3
unnamed: R1019.1, R1020.2
unnamed: R1022.1, R1024.2, U1009.1
unnamed: R1023.1, R1025.1
unnamed: R1028.2, U1014.4
unnamed: C1027.1, T1001.1 (AA)
unnamed: C1022.1, T1001.3 (SA)
unnamed: C1021.1, T1001.4 (SB)
unnamed: C1028.1, T1002.1 (AA), TP1002.1
unnamed: C1015.1, U1001.5 (CLPF)
unnamed: R1010.2, R1012.2, U1001.16 (ENBL)
unnamed: R1004.1, U1001.10 (TADJ)
unnamed: R1013.2, U1001.13 (TEMP)
unnamed: R1015.2, U1001.6 (VOUT)
unnamed: C1020.1, R1008.1, U1001.9 (VPSO)
unnamed: U1001.7 (VSET), U1003.3
unnamed: C1025.1, U1002.3 (INHI)
unnamed: C1026.2, U1002.4 (INLO)
unnamed: C1014.2, U1002.8 (IPBS)
unnamed: C1009.2, U1002.9 (OPBS)
unnamed: C1016.2, U1002.7 (VREF)
unnamed: U1003.1, U1004.1
unnamed: L1005.1, U1006.18 (IREF)
unnamed: C1032.1, R1020.1, U1006.1 (VBIAS)
unnamed: R1021.1, R1022.2, U1009.2 (-)
unnamed: C1043.2, U1012.4 (IN)
unnamed: U1012.8 (OUT), U1018.5 (RF1)
unnamed: C1049.2, U1013.2 (RFIN)
unnamed: C1042.2, L1009.1, U1013.7 (RFOUT)
unnamed: R1028.1, R1029.1, U1013.6 (Shut_Down)
unnamed: U1015.4 (IN), U1018.11 (RF2)
unnamed: C1049.1, U1015.8 (OUT)
unnamed: R1033.1, U1016.3 (ISET)
unnamed: NT1001.2, U1016.2 (PGOOD)
unnamed: R1032.1, U1017.3 (ISET)
unnamed: NT1002.2, U1017.2 (PGOOD)
unnamed: C1055.2, U1018.2 (RFC)

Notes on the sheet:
3.3->OFF
LOW->PIN3 HIGH->PIN1
(0-1.4)V
the resistor values should be kept as low as possible to ensure that leakage current effects have minimal impact. The power consumption of the resistor divider network ultimately decides how low a resistance is tolerable
(0-5)V
Alternative part XS3A1T3157 with same footprint
5.0->ON (8.9mA)
Current limit: 2.5A
Current limit: 0.74A
In series R > R to GND
(0.5-2.1)V, Absolute Max 5V
EN->ON->3.3 Vctl->0->RF1->TX Vctl->3.3->RF2->RX
(0-3.3)V
(0-1)V

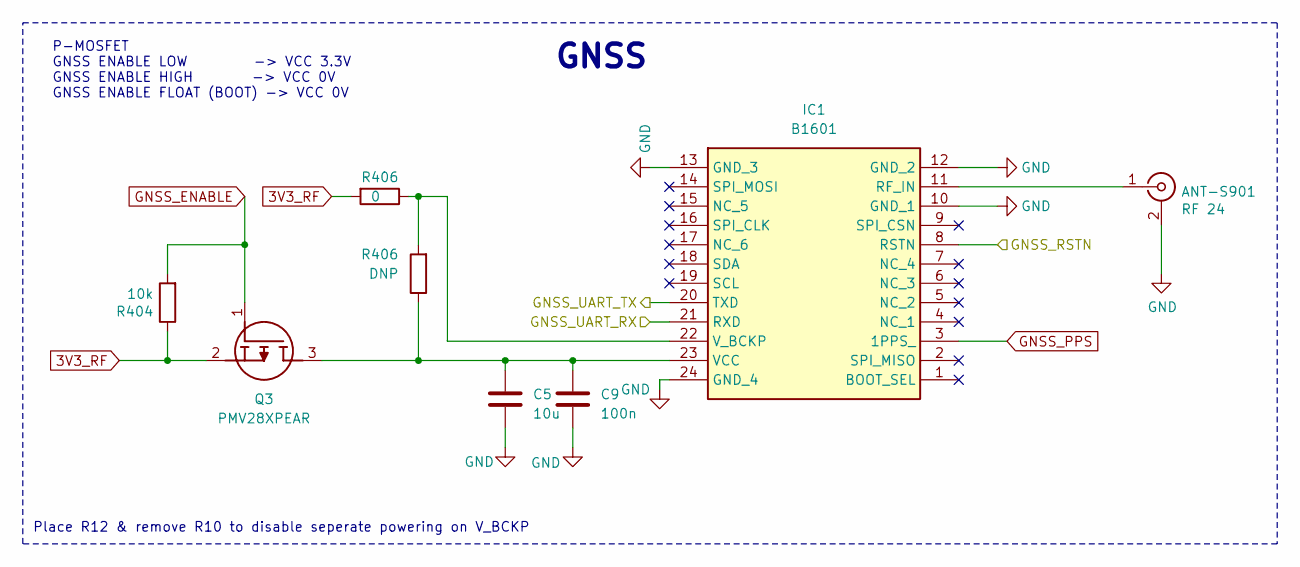
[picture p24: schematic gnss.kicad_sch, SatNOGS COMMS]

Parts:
ANT-S901: RF 24; MMCX_Molex_73415-0961_Horizontal_1.6mm-PCB; PartNumber 73415-0961
C5: 10u; C_0603_1608Metric
C9: 100n; C_0603_1608Metric
IC1: B1601; Manufacturer_Part_Number B16‐01
Q3: PMV28XPEAR; SOT95P230X110-3N; Mouser Part Number 771-PMV28XPEAR
R404: 10k; R_0402_1005Metric; PartNumber CRCW040210K0FKEDC
R406: DNP; R_0402_1005Metric; PartNumber CRCW040210K0FKEDC

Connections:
/MCU/GNSS_RSTN: IC1.8 (RSTN); also elsewhere on the board
/MCU/GNSS_UART_RX: IC1.21 (RXD); also elsewhere on the board
/MCU/GNSS_UART_TX: IC1.20 (TXD); also elsewhere on the board
GNSS_ENABLE: Q3.1 (G); also elsewhere on the board
GNSS_PPS: IC1.3 (1PPS_); also elsewhere on the board
unnamed: ANT-S901.1 (In), IC1.11 (RF_IN)

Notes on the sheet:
Place R12 & remove R10 to disable seperate powering on V_BCKP
GNSS
P-MOSFET GNSS ENABLE LOW -> VCC 3.3V GNSS ENABLE HIGH -> VCC 0V GNSS ENABLE FLOAT (BOOT) -> VCC 0V

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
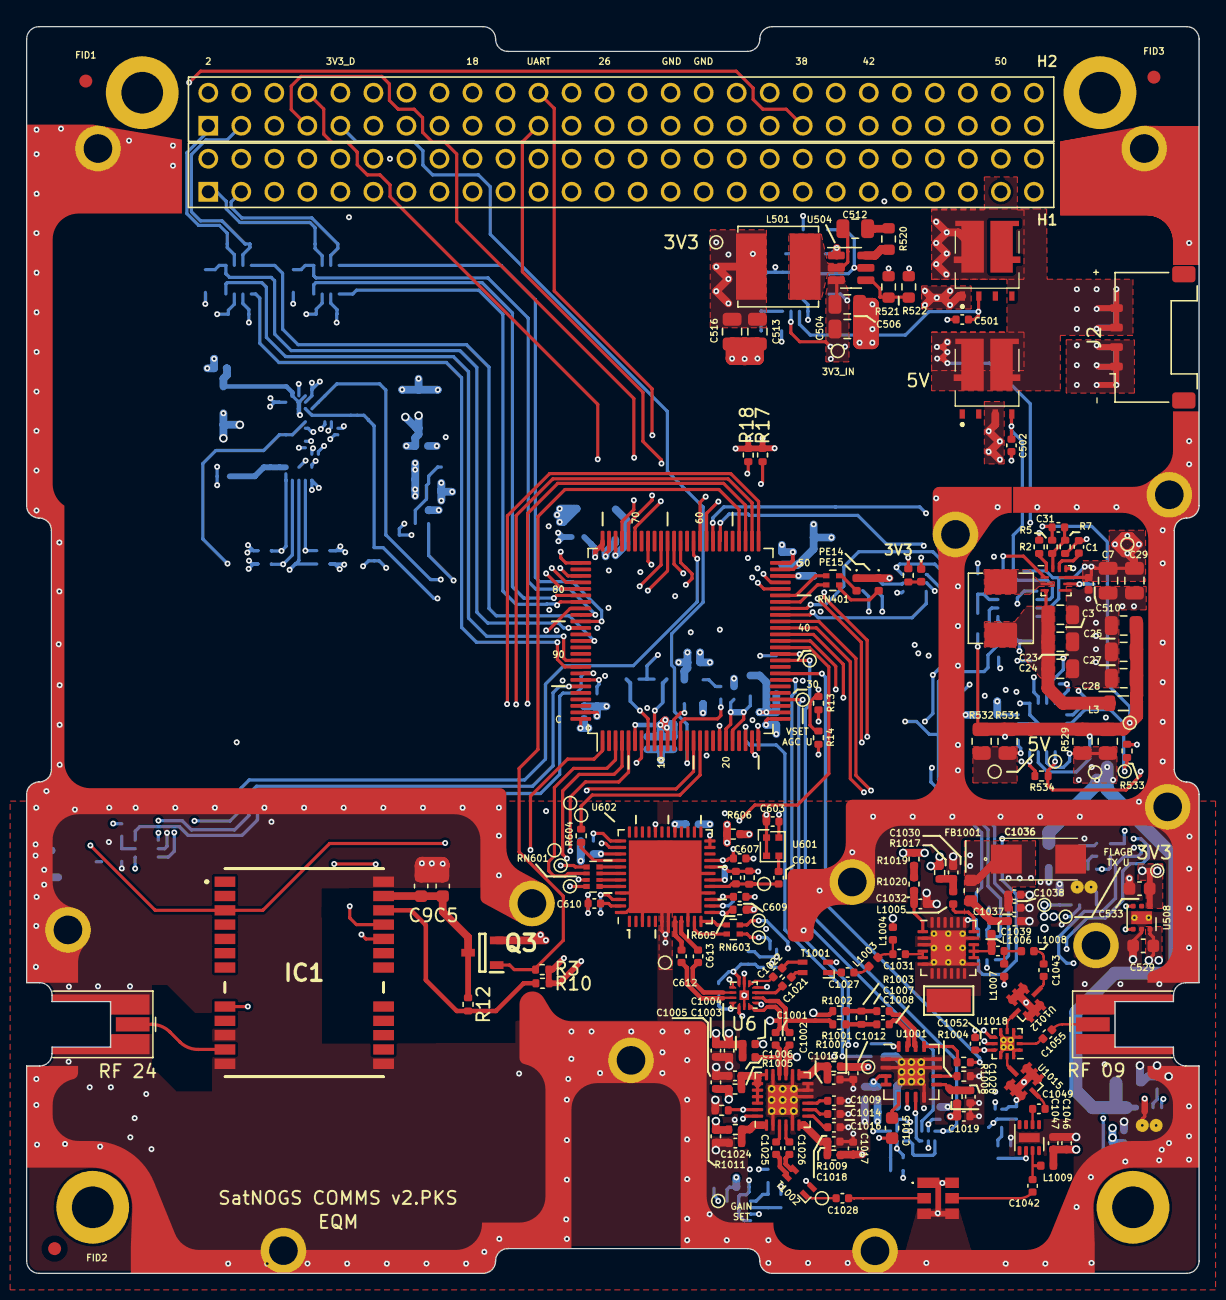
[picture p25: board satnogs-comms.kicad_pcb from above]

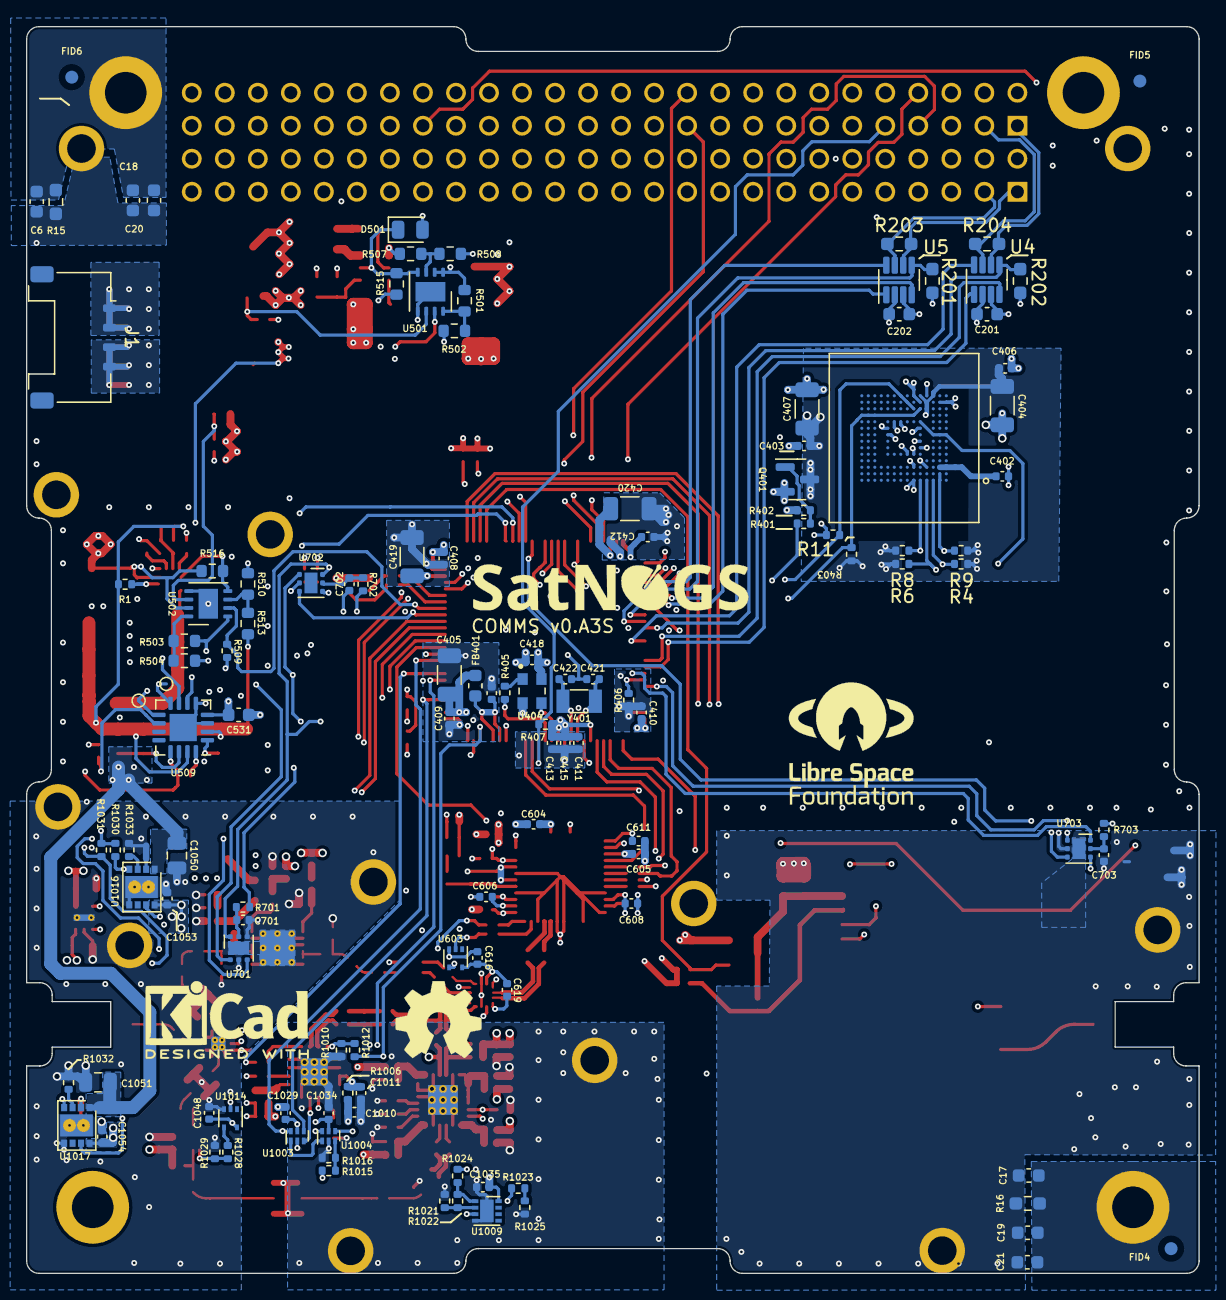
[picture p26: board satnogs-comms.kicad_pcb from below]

Board: 6 copper layers, 90.2 x 95.9 mm, 315 parts (126 on the bottom side), 202 nets.

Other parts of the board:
C1: 470n; C_0402_1005Metric
C3: 22uF; C_0805_2012Metric
C7, C29: 6.8u; C_0805_2012Metric
L2: 2.2u; L_Abracon_ASPI-0530HI
R2: 18.2k; R_0402_1005Metric
R3: 10k; R_0402_1005Metric
R5: 25.5k; R_0402_1005Metric
R7: 4.87k; R_0402_1005Metric
R10: 0; R_0402_1005Metric
R12: DNP; R_0402_1005Metric
U3: TPS62913; Texas_VQFN-10-HR_2x2_Pitch0.5mm

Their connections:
GNSS_ENABLE: R3.2; also elsewhere on the board
unnamed: R2.1, U3.10 (S-CONF)
unnamed 140: R5.1; also elsewhere on the board

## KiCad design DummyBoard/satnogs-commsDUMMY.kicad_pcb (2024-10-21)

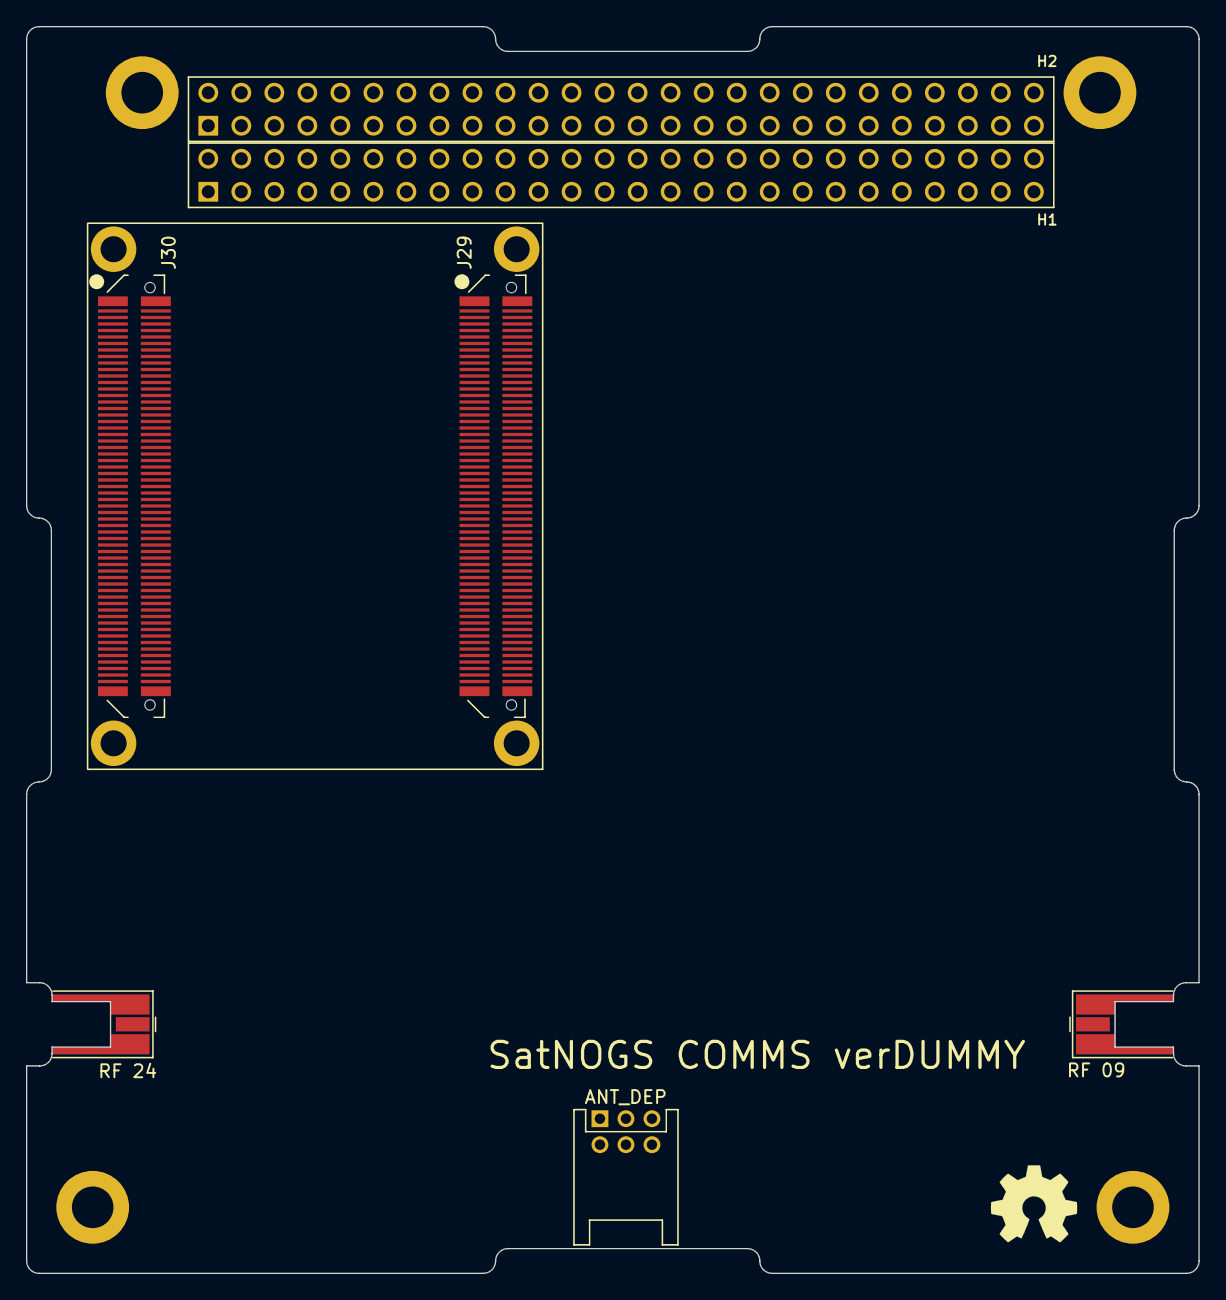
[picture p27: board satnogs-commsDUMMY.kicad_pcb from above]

Board: 2 copper layers, 90.2 x 95.9 mm, 10 parts (0 on the bottom side), 4 nets, no tracks yet.

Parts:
ANT-S901: RF 24; MMCX_Molex_73415-0961_Horizontal_1.6mm-PCB
ANT-U1001: RF 09; MMCX_Molex_73415-0961_Horizontal_1.6mm-PCB
H111, H112, H113, H114: MountingHole_Pad; MountingHole_3.2mm_M3_DIN965_Pad
J101: ANT_DEP; hrs-df11-6dp-2ds
J102: Η1; ESQ-126-39-x-D
J103: Η2; ESQ-126-39-x-D
U301: Alinx_ZYNQ-7000_SOM_XC7Z020

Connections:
2V5_FPGA: U301.12 (VCCIO_35), U301.14 (VCCIO_35), U301.16 (VCCIO_35), U301.18 (VCCIO_35)
3V3_FPGA: U301.11 (VCCIO_34), U301.13 (VCCIO_34), U301.15 (VCCIO_34), U301.17 (VCCIO_34)
5V_FPGA: U301.1 (VCC5V), U301.2 (VCC5V), U301.3 (VCC5V), U301.4 (VCC5V), U301.5 (VCC5V), U301.6 (VCC5V), U301.7 (VCC5V), U301.8 (VCC5V)
GND: ANT-S901.2 (Ext), ANT-U1001.2 (Ext), J101.5, J101.6, J102.33, J102.34, J103.29, J103.30, J103.31, J103.32, U301.9 (GND), U301.10 (GND), U301.19 (GND), U301.20 (GND), U301.29 (GND), U301.30 (GND), U301.39 (GND), U301.40 (GND), U301.49 (GND), U301.50 (GND), U301.59 (GND), U301.60 (GND), U301.69 (GND), U301.70 (GND), U301.79 (GND), U301.80 (GND), U301.89 (GND), U301.90 (GND), U301.99 (GND), U301.100 (GND), U301.109 (GND), U301.110 (GND), U301.129 (GND-T13), U301.130 (GND-T13), U301.139 (GND-T13), U301.140 (GND-T13), U301.149 (GND-T13), U301.150 (GND-T13), U301.159 (GND-T13), U301.160 (GND-T13), U301.169 (GND-T13), U301.170 (GND-T13), U301.179 (GND-T13), U301.180 (GND-T13), U301.189 (GND-T13), U301.190 (GND-T13), U301.199 (GND-T13), U301.200 (GND-T13), U301.209 (GND-T13), U301.210 (GND-T13), U301.219 (GND-T13), U301.220 (GND-T13), U301.229 (GND-T13), U301.230 (GND-T13)

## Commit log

2024-04-11 Finalised Schematic
    [MCU.kicad_sch, gnss.kicad_sch, main_psu.kicad_sch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]
2024-04-15 Resolved issues
    [MCU.kicad_sch, gnss.kicad_sch, satnogs-comms.kicad_sch]
2024-04-16 Updated PC104 connector
    [satnogs-comms.kicad_sch]
2024-04-17 Fixed all ERC Errors & Warnings
    [ATB2012.FCStd, CONMCX001.FCStd, D2F-L.FCStd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]
2024-04-17 Updated all footprints
    [CAN.kicad_sch, MCU.kicad_sch, RF.kicad_sch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]
2024-04-18 Added Molex footprints
    [RF.kicad_sch, gnss.kicad_sch, satnogs-comms.kicad_sch]
2024-04-19 Finished layout
    [RF.kicad_sch]
2024-04-19 Resolved errors
    [satnogs-comms.kicad_sch]
2024-04-22 changed vias to burried in BGA region
    [satnogs-comms.kicad_pcb]
2024-04-22 Added missing shield
    [satnogs-comms.kicad_pcb]
2024-04-22 Resolve issues #6-#8
    [MCU.kicad_sch, RF.kicad_sch, gnss.kicad_sch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]
2024-04-22 Silkscreen update
    [satnogs-comms.kicad_pcb]
2024-04-22 Gerbers updated
    [satnogs-comms-B_Cu.gbl, satnogs-comms-B_Cu.gbr, satnogs-comms-B_Mask.gbr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]
2024-04-22 Minor Update
    [satnogs-comms-B_Cu.gbr, satnogs-comms-B_Mask.gbr, satnogs-comms-B_Paste.gbr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]
2024-04-22 Remove Test points
    [satnogs-comms.kicad_pcb]
2024-04-25 Silkscreen updates
2024-04-29 Generated BOM
    [COMMS_BOM.xlsx, bom.xls]
2024-10-11 PCB: PC104 Update
    [CAN.kicad_sch, MCU.kicad_sch, RF.kicad_sch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]
2024-10-21 PSU: Add 2.2u soft-start capacitor on RF DCDC converter
    [5040500491.stp, ASPI-0530HI-2R2M-T2.stp, B16тАР01.stp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]
2024-10-21 Add SWOTRACE pin to PC104
    [MCU.kicad_sch, satnogs-comms.kicad_sch]
2024-10-21 PCB: Expose BOOT selection pin
    [MCU.kicad_sch]
2024-10-22 Add FM Gerbers
2024-10-29 Update FM BOM
    [COMMS_BOM.xlsx, main_psu.kicad_sch]
2024-11-27 Update BOM
    [COMMS_BOM.xlsx, COMMS_FM_BOM.xlsx, uhf-frontend.kicad_sch]

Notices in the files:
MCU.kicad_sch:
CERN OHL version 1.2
